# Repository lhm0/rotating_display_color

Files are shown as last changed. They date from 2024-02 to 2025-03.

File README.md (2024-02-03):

# Rotating Color Display

## Abstract: 
 The Rotating Color Display is a compact disc-sized device that rotates quietly using a CD motor. It features 56 color LEDs that display animated color images as well as time and weather data sourced from the internet. The device is wirelessly powered and controlled via a user-friendly web interface. It uses ESP32 and RP2040 microcontrollers, pre-manufactured boards, and is easy to assemble.
 
<p align="center"> 
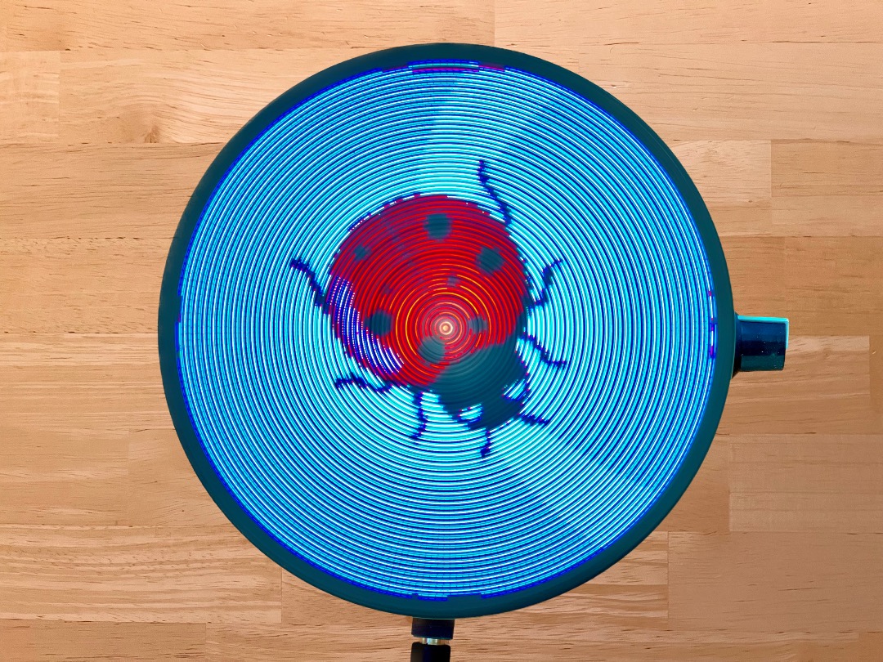
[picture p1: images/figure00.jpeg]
  
</p>

<p align="center"> 
<a href="https://youtu.be/7XahXYzULtI?si=OmdDaNnT-Jkq3F4Q" target="_blank">
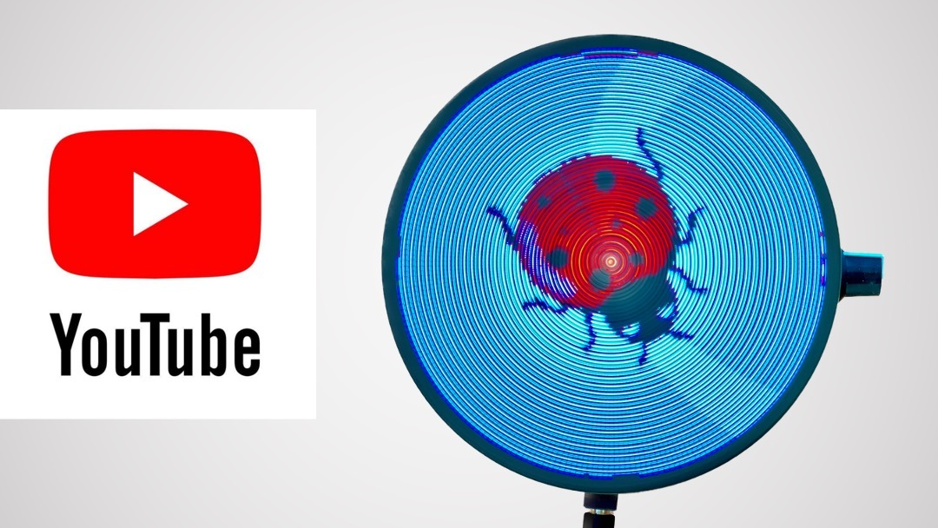
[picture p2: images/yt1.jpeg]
  
</a>
</p> 

## 1. Description of the device

The Rotating Color Display device comprises two primary units: a power supply unit and a display board (**figure 1**). Both are circular in design, with a diameter of 120mm, similar to the dimensions of a standard Compact Disk. The display board is rotated by a CD motor. Energy is wirelessly transmitted from the power supply unit to the display board, eliminating the need for wired connections.

<p align="center"> 
  
</p>

**Figure 1:  Rotating Color Display assembly.** The lower PCB is the power supply with wireless power transmission, the upper PCB is the display board.

The display board is equipped with a row containing 56 color LEDs. The LED operations are controlled by a RP2040 microcontroller, while an ESP32 microcontroller generates the display content. Images (including animated images) can be stored on and loaded from a micro SMD card. The ESP32 maintains a Wi-Fi connection to the internet.

This internet connection allows the device to retrieve the time from a time server, ensuring time accuracy. It also allows for the acquisition of weather data. Device operation is managed through a web interface (**figure 2**), accessible from any web browser. The interface allows users to manage login credentials, upload image files to the display, and control image and configuration files through a file manager.

<p align="center"> 
  
  
  
</p>
<p align="center"> 
  
  
  
</p>

**Figure 2:** The **web user interface** allows for operating mode selection and device configuration.

## 2. Operating modes

When switched on, the device tries to connect to a known wifi. If no valid wifi credentials are found, the unit will be configured as wifi access point. In this mode, a computer or mobile device can be connected, directly (SSID: RD40, no password). 

Once the wifi connection has been established, the unit will display its IP address on the  home page of the device (**figure 3**). Enter this address in your web browser. This will load the web user interface and will allow you to configure your local wifi.

<p align="center"> 
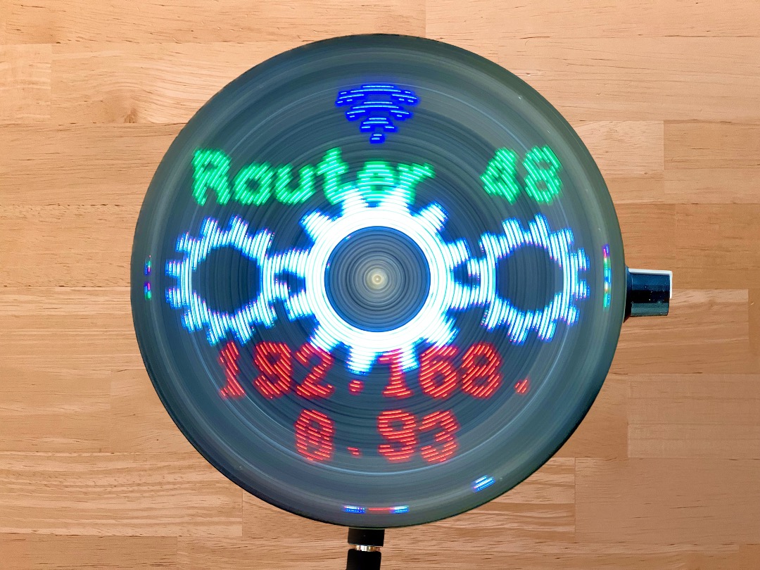
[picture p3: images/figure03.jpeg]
  
</p>

**Figure 3: home page.**

There are several operating modes that display time and weather information (**figure 4**). The logo clock mode integrates a customizable image into the clock face. The image can be easily uploaded from the user interface. The same is true for the analog clock, which uses a customizable clock face in the background.

<p align="center"> 
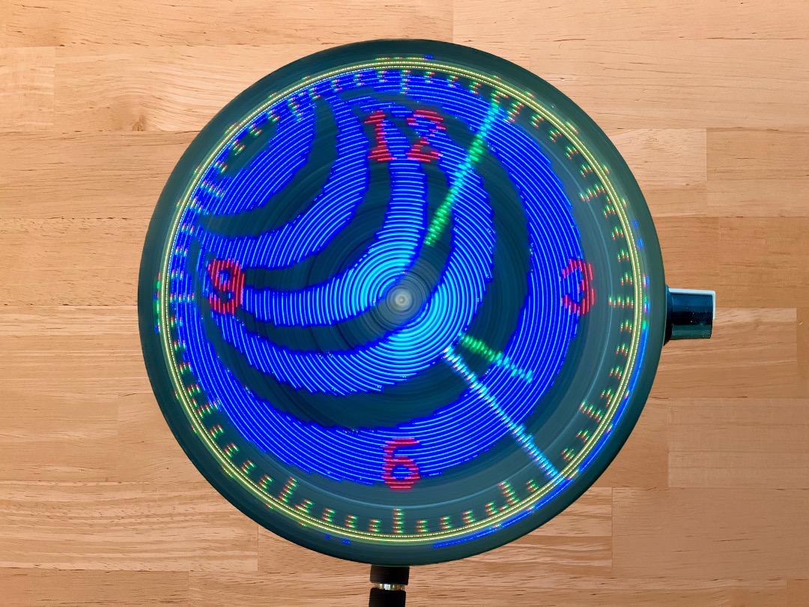
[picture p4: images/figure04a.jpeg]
  
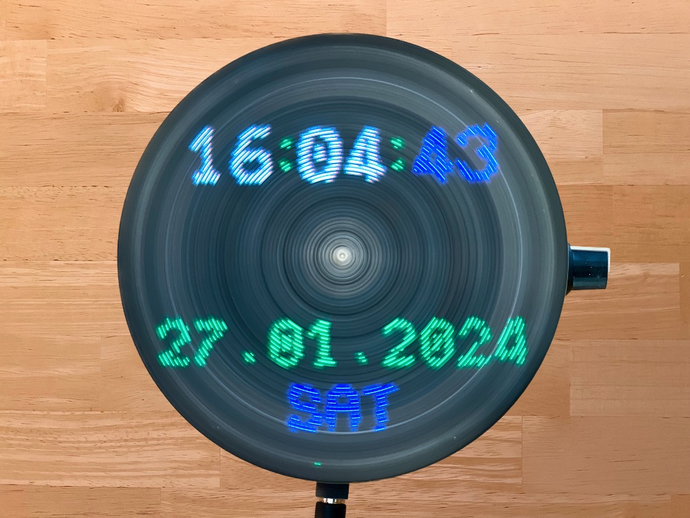
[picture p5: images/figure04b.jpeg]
  
</p>
<p align="center"> 
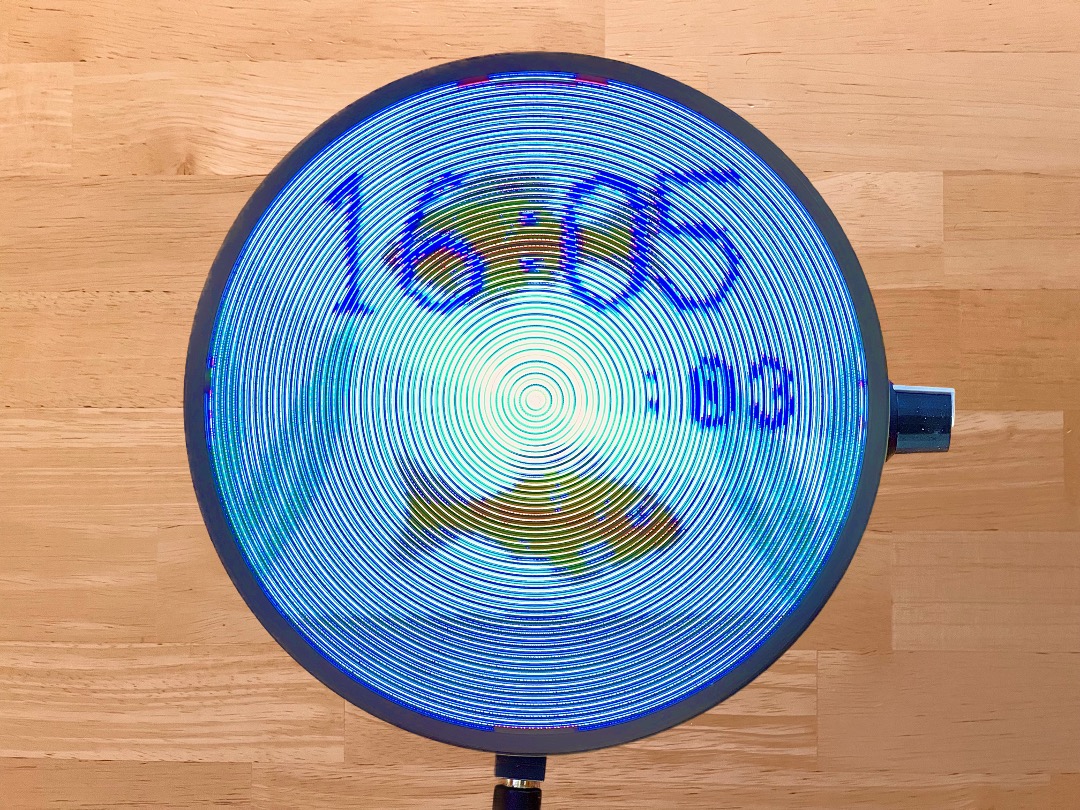
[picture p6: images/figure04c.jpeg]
  
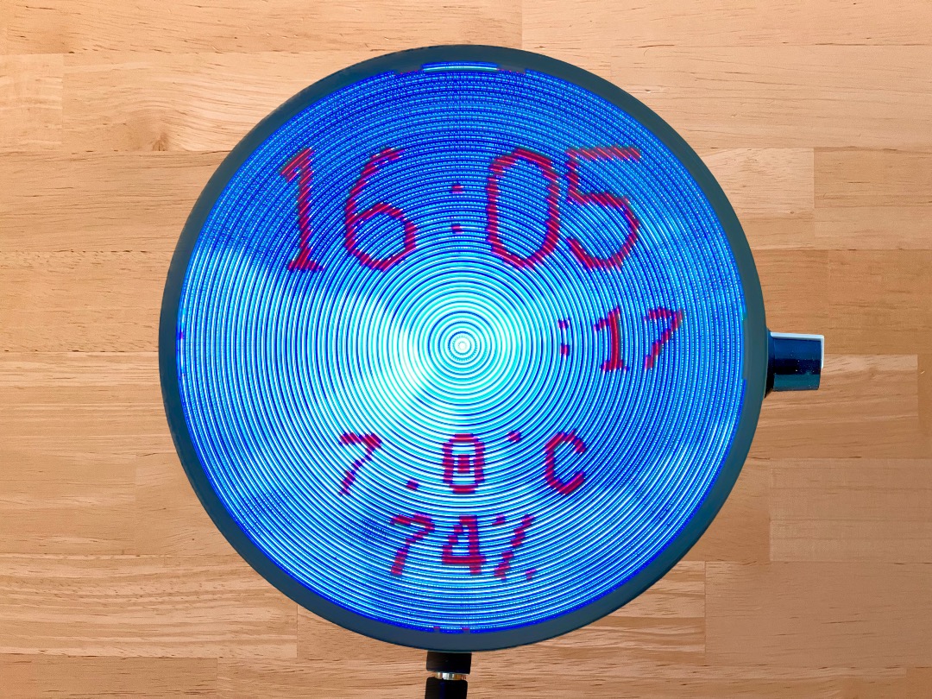
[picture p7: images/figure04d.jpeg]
  
</p>

**Figure 4: operating modes.** Modes can be selected and configured through the web interface.

## 3. Mechanical design

The device consists of two assemblies: power supply and display. The power supply board is also the base plate, which can either be placed on a flat surface or hung on a wall. A standard CD motor is attached to this board so that the CD tray above the power supply board can accommodate the display assembly. The display board is fixed with two M2 x 6 mm screws. Furthermore, the base plate carries a potentiometer to control the motor speed as well as an on/off switch for the motor.

<p align="center"> 
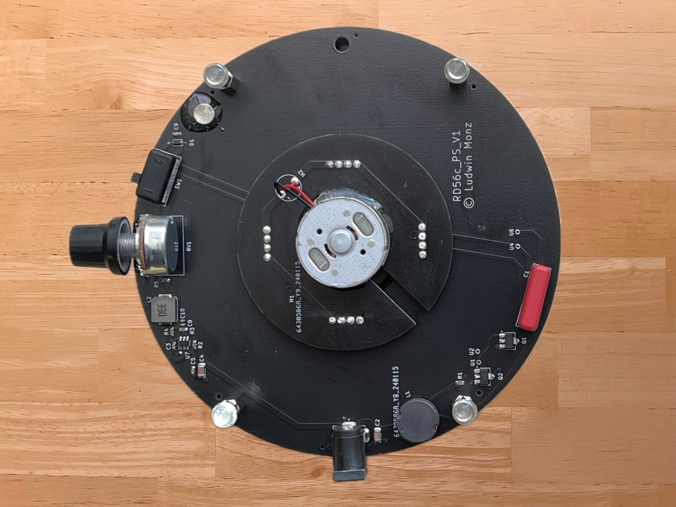
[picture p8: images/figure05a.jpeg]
  
  
</p>

**Figure 5: Power Supply Board** with CD motor (middle), 12 - 24 V power jack (lower side), and speed potentiometer

An important requirement for the display board is that the center of mass of the unit is exactly in the middle, on the axis of rotation of the motor. This is the only way to ensure smooth and vibration-free running of the display. To achieve this, the electronic components are arranged symmetrically in three groups (**figure 7**). In the first group the components are arranged symmetrically to a vertical axis. This initially ensures that the center of gravity lies on this vertical axis. However, since the components cannot be distributed symmetrically to the horizontal axis of symmetry, the center of gravity must be shifted to the center along this axis using balancing weights. For this purpose, two M3x6mm screws with two nuts each are placed to the right and left of the ESP32 antenna. The second group of components is arranged symmetrically in respect to the center point of the disk and does not need a balancing weight, therefore. The third group, however, does need a balancing weight (M3 x 6, 1 nut) in the 4:30 position of the disk.The overall balancing result is very good, but can certainly be further optimized.

<p align="center"> 
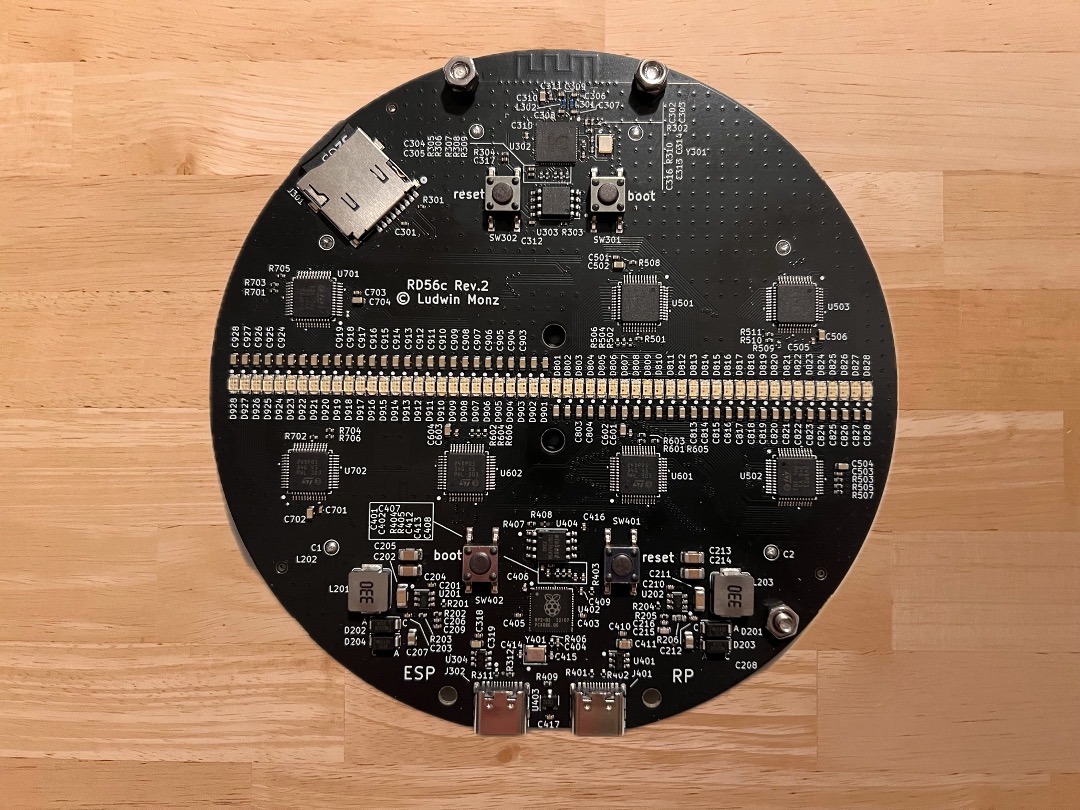
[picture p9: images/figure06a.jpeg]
  
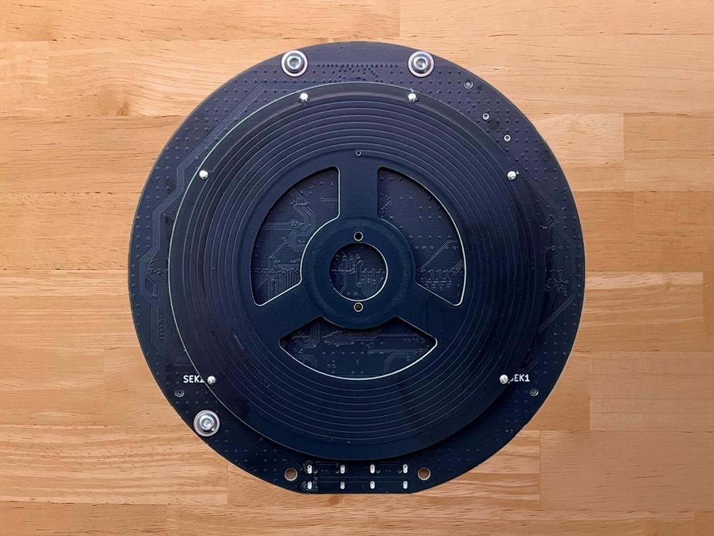
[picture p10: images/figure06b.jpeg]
  
</p>

**Figure 6: Display Board.** Main components are the two LED rows, five serial shift register chips, and two microcontrollers (Arduino nano and ESP-01s). On the backside of the board the secondary coil of the wireless power supply is attached.

<p align="center"> 
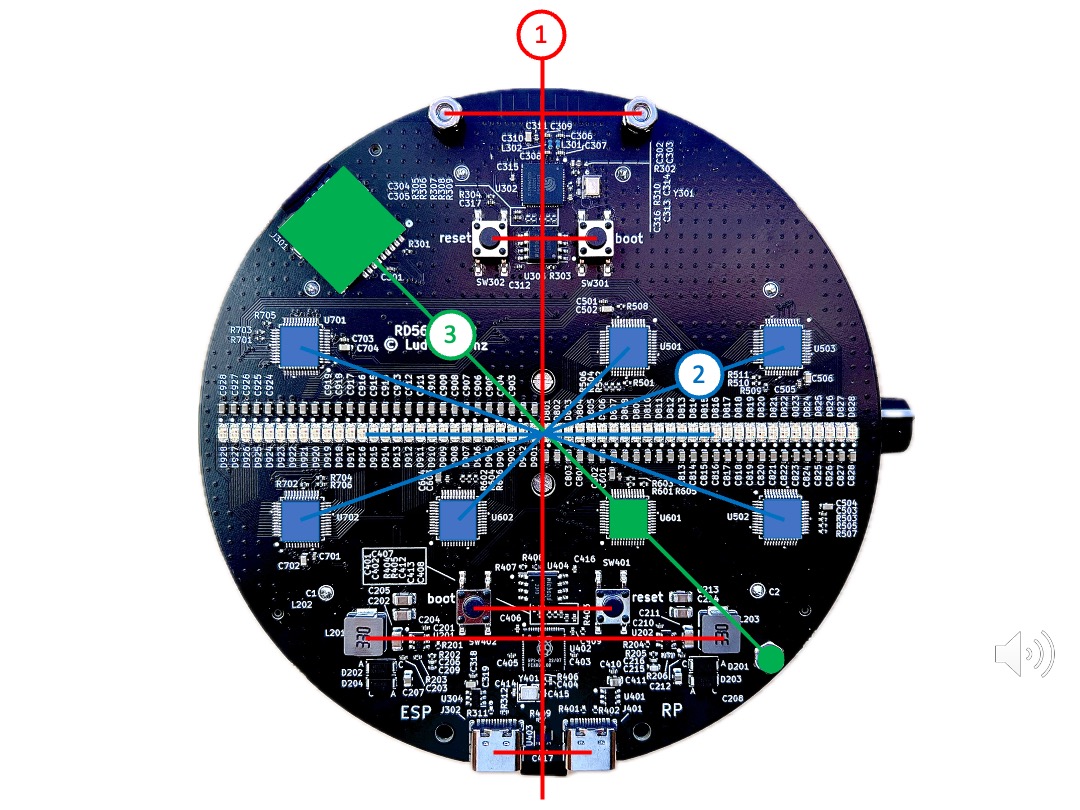
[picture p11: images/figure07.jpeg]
  
</p>

**Figure 7:** The components of the display board are arranged symmetrically in three groups. Balancing weights are used in group 1 and 3 to shift the center of gravity to the middle of the disk.

The LED row consists of 56 discrete, rectangular LEDs. The components each have a width of 1.6 mm and can be lined up with little spacing. The center of the LEDs is in a 2 mm grid. However, the row of LEDs is not arranged symmetrically to the center of the disk, but shifted by 0.5 mm. If the display panel is rotated by 180 degrees, this decentration causes the LEDs to be shifted by exactly 1 mm from the original grid (**figure 8**). This results in rotational interlacing: the radial resolution is increased from 2 to 1 mm. At the same time, the perceived frame rate also increases by a factor of 2..

<p align="center"> 
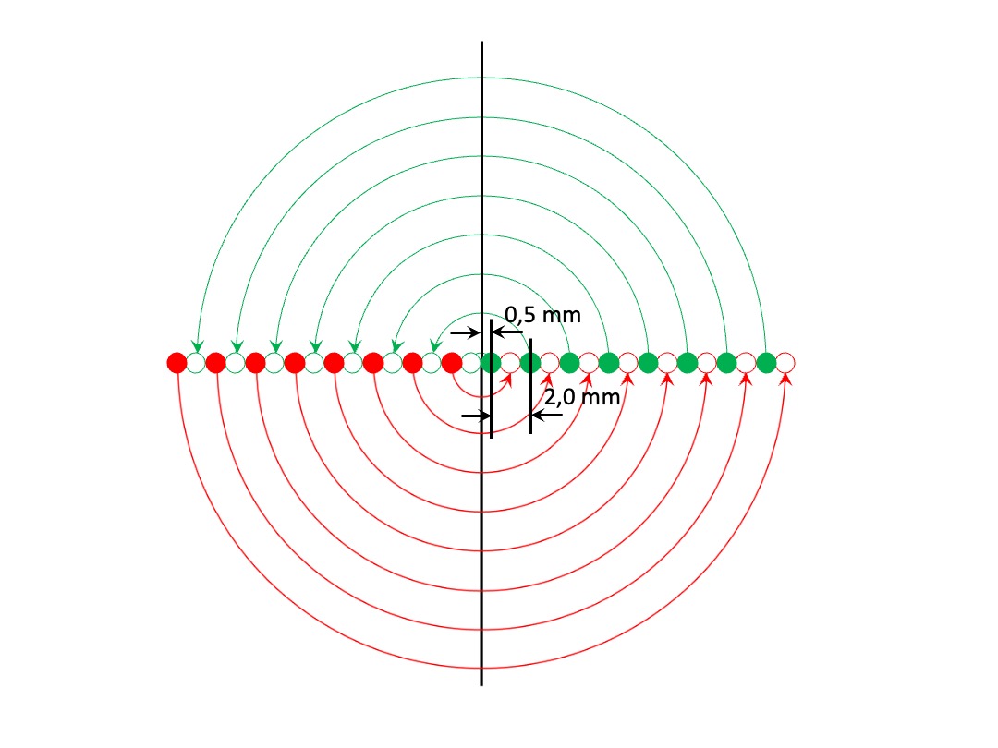
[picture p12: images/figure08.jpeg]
  
</p>

**Figure 8:** The LED row is shifted radially by half a LED width. The two halfs of the row generate an interlacing effect, which doubles both the radial resolution and the image frame rate.

The LEDs must output the image information at exactly the right position with each rotation. For spatial alignment of the image, a trigger signal is generated at a defined position for each rotation, which triggers the sequential, clocked output of the pixels. The trigger signal must be spatially very stable, otherwise no smooth image can be generated. It turned out that a Hall sensor is best suited for this purpose. It is located between the two USB-C connectors (see **figure 6**, left picture, bottom edge of the PCB). The magnet is glued into a hole of the power supply PCB (see figure 5, right picture, 2 o'clock position).

## 4. Electronics architecture

The distribution of the electronic circuitry between the two assemblies is shown in **figure 9**. The power supply assembly contains a Royer converter for wireless power transfer to the display assembly and an adjustment of the motor speed. The 56 color LEDs of the display assembly are controlled by 7 shift registers (24 bits each), which in turn are supplied with clock and data by a RP2040 microcontroller via an SPI interface. The displayed content is generated by an ESP32-S3 microcontroller, which is connected to the internet via Wifi. Furthermore, image data can be loaded from a micro SD card. The ESP32 transmits its data to the RP2040 via a SPI interface.

<p align="center"> 
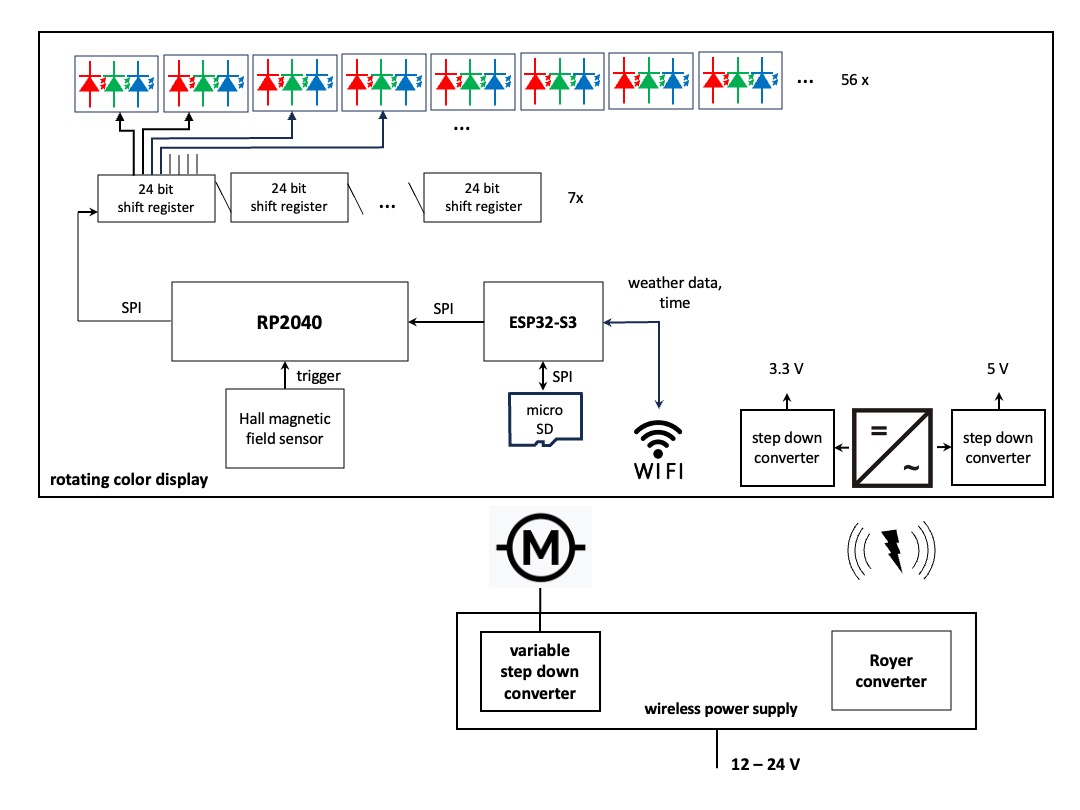
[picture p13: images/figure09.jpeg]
  
</p>

**Figure 9: electronics schematics.**

## 5. Power supply board

The core of the power supply is a Royer converter for wireless power transfer. An excellent article on the operation and design of the circuit can be found at Mikrocontroller.net (German) and the circuit was taken from there. Two transistors are alternately switched (push pull operation) so that a current flows through one half of the coil at a time. The coil belongs to a resonant circuit with a resonant frequency of about 120 kHz. The control voltage for the transistors is obtained via a coupling coil (**figure 10**). The secondary coil is located below the display board (see **figure 6**, right).

The Royer circuit uses very few components. However, the coil is quite complex. It is a bifilar coil, where the two halves are interleaved. In addition, the coupling coil must be connected with the correct polarity, otherwise the two transistors will be destroyed. In the early stages of development, the coil was wound with copper wire. However, this solution was quite difficult to reproduce, so in the final design the coils (bifilar primary coil, coupling coil, secondary coil) were implemented as a printed circuit (see **figure 5**, right and **figure 6** right). The circuit was found to have surprisingly high and perfectly adequate transmission efficiency, although the quality factor of the printed coils is inevitably compromised. The Royer converter with the printed coil assembly is absolutely safe to rebuild.

The Royer converter can be supplied with 12 to 24 V. Depending on the voltage, the transferred power can be increased. This allows the operation of the display at high brightness. However, even with 12 V supply, the available power is sufficient for normal operation. 

<p align="center"> 
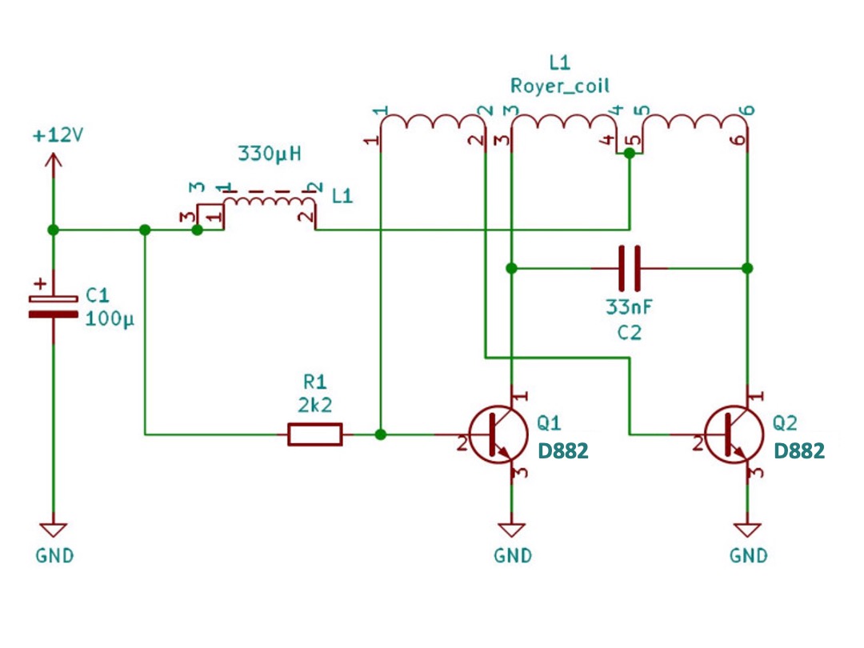
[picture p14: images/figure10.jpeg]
  
</p>

**Figure 10: Royer converter**. Compare Mikrocontroller.net for reference.

There is also a circuit for supplying the CD motor on the power supply board (**figure 11**). As the supply voltage can be vary from 12 to 24 V, a step down converter is used to generate a variable voltage between 1.7V and 6.0V, which can be adjusted via a potentiometer. The voltage range corresponds to the specified operating range of the CD motor. The supply of the motor can be interrupted with a switch, for example to allow programming of the microcontrollers.

<p align="center"> 
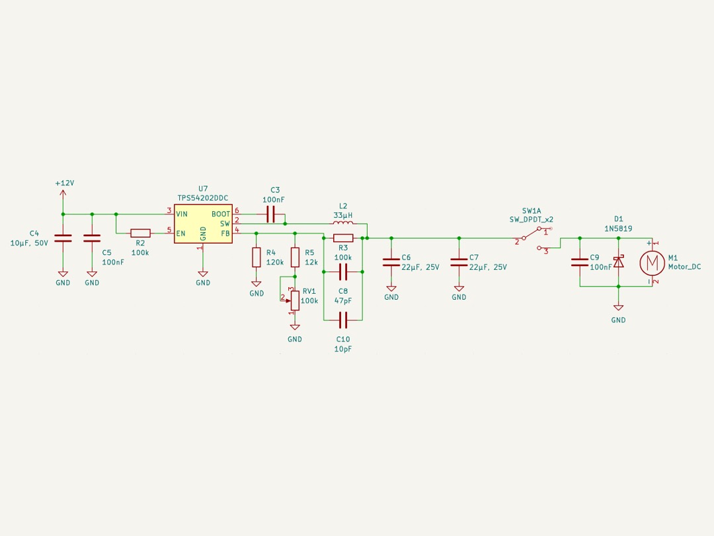
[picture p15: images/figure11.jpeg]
  
</p>

**Figure 11: variable voltage regulator** for driving the CD motor

## 6. Display Board

**a) The LEDs**

The 56 LEDs of the display board are driven by 7 cascaded 24-bit shift registers (**figure 12**). The registers load the serial data stream from one of the SPI interfaces of the RP2040. The microcontroller generates separate "LED enable" signal for the R, G, B LEDs, respectively. This allows for white balancing (not implemented yet). The STP24DP05BTR LED current sink controller sets the LED current to 20mA each. The maximum current per register would therefore be 480mA, if all LEDs were on, simultaneously and continuously. Theoretically, the current of the 56 LEDs could add up to 3.3A, which, at 5V, would correspond to 16.5 W. This is significantly beyond the capability of the wireless power supply. However, the current can be controlled by the RP2040 microcontroller by setting the duty cycle appropriately.

<p align="center"> 
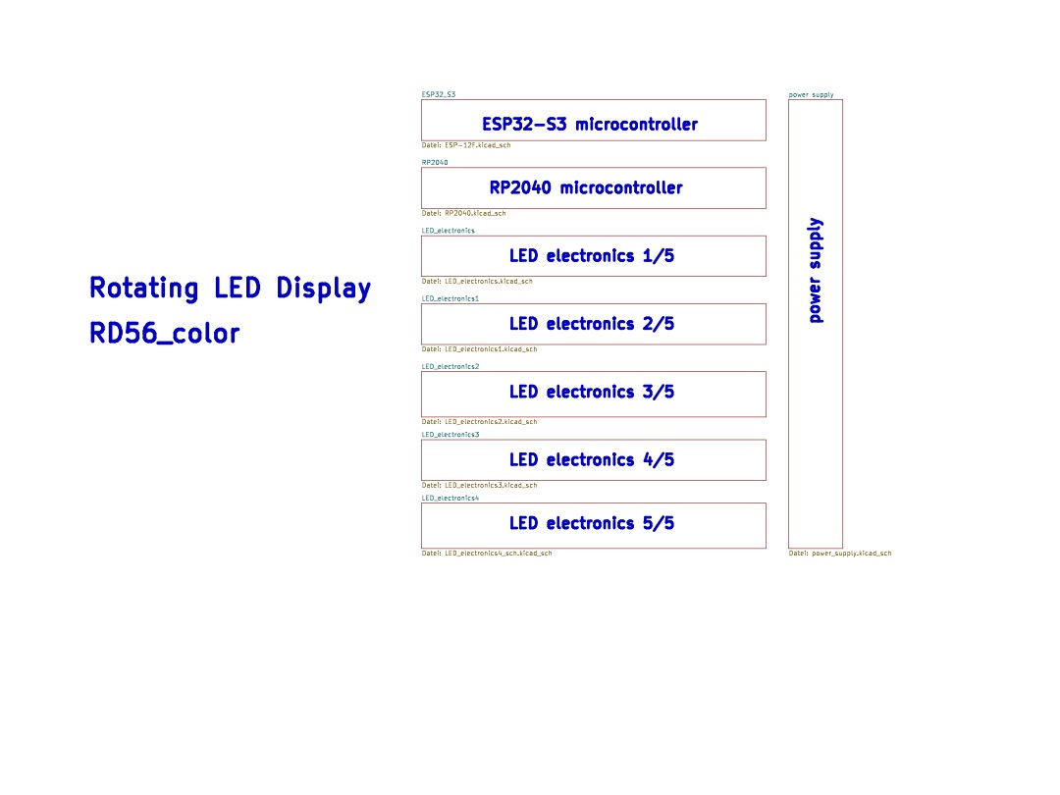
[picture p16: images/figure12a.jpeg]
  
</p>
<p align="center"> 
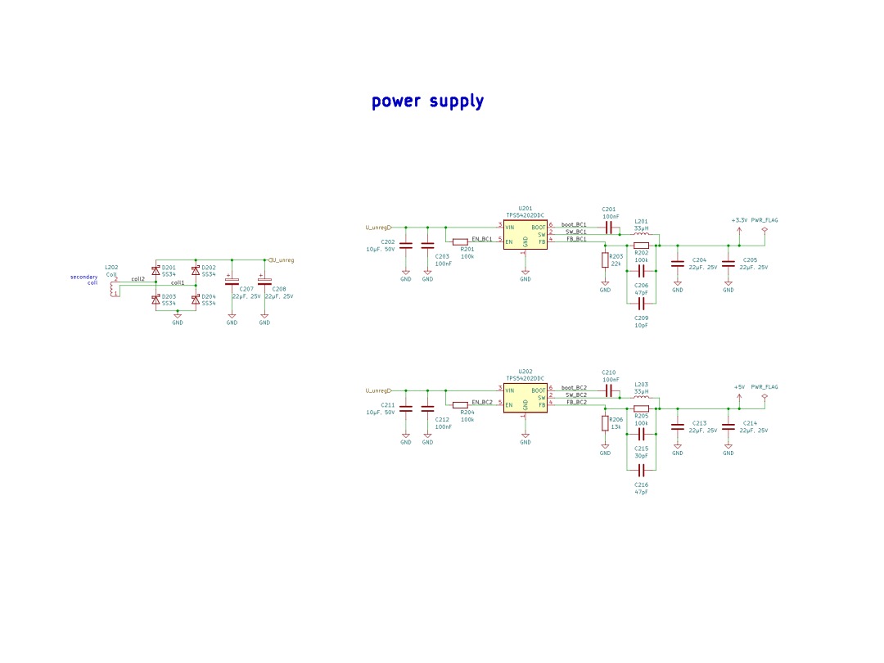
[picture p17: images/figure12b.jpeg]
  
</p>
<p align="center"> 
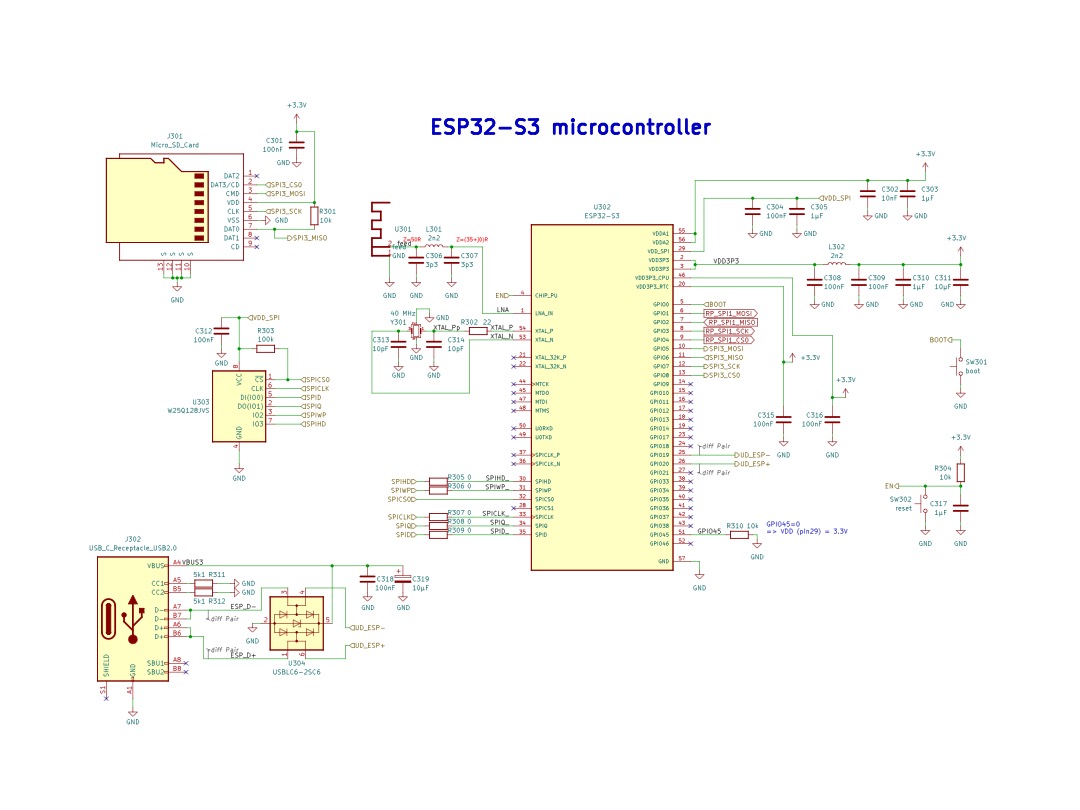
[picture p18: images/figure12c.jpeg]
  
</p>
<p align="center"> 
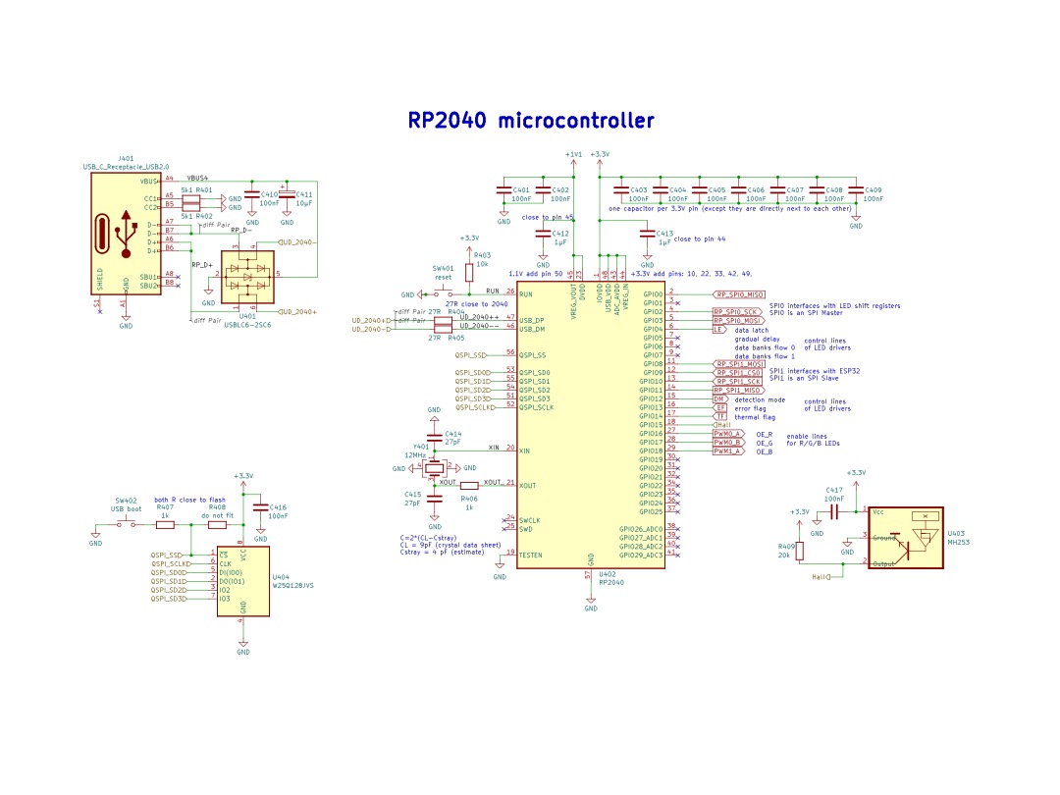
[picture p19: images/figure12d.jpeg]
  
</p>
<p align="center"> 
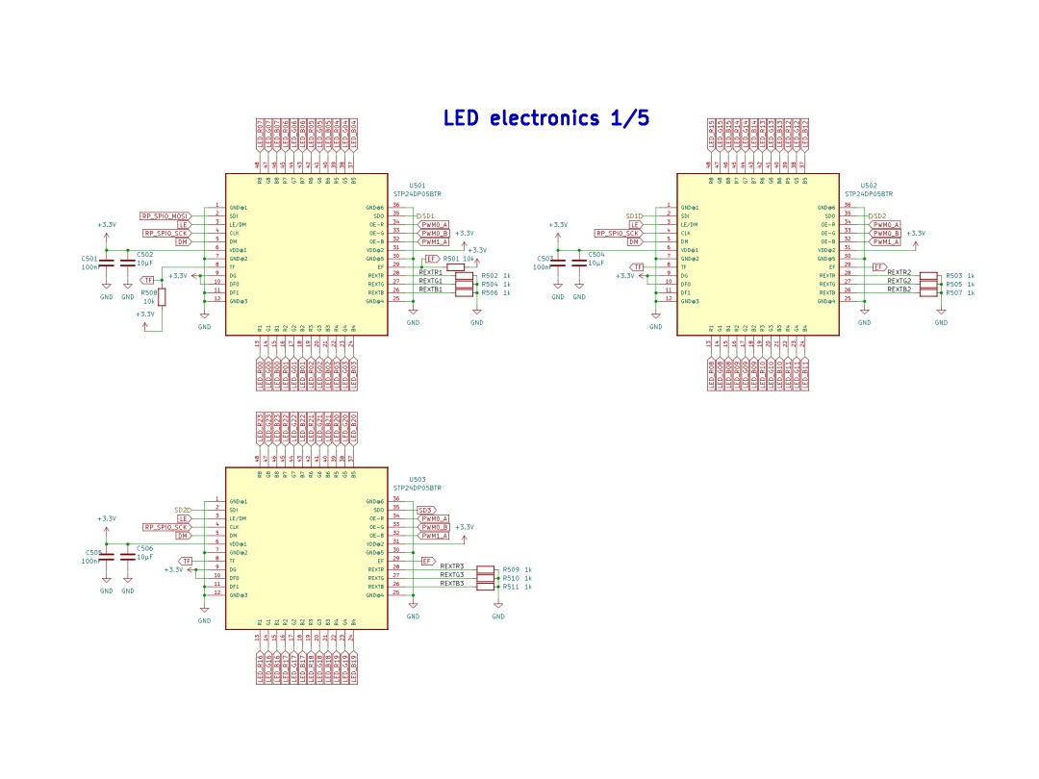
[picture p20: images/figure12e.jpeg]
  
</p>
<p align="center"> 
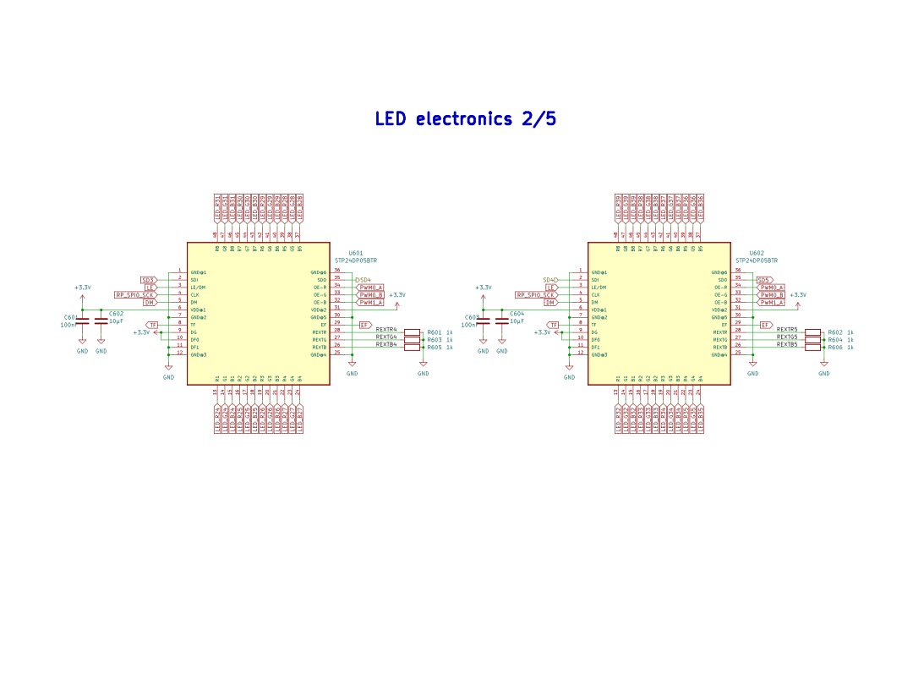
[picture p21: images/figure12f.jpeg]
  
</p>
<p align="center"> 
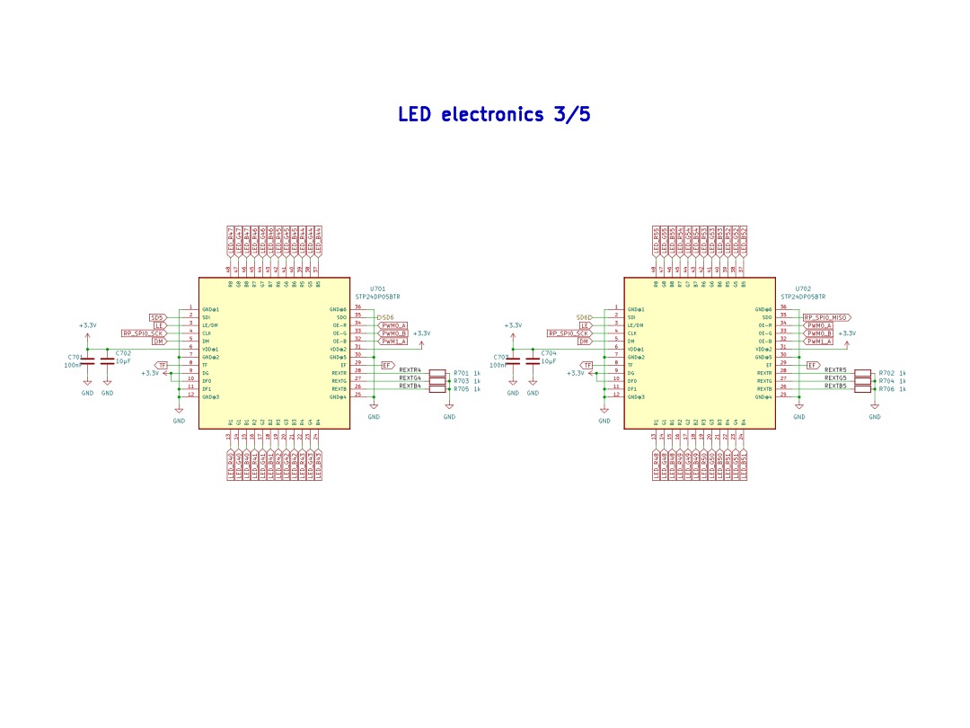
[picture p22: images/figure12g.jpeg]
  
</p>
<p align="center"> 
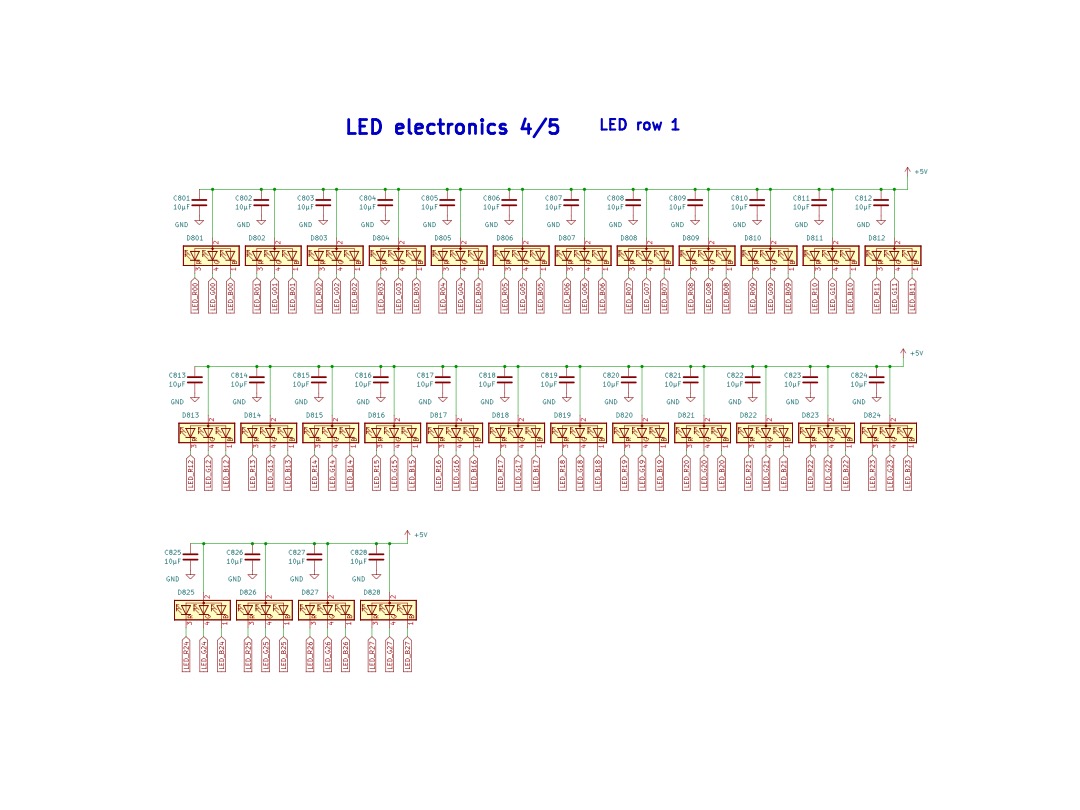
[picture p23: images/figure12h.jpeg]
  
</p>
<p align="center"> 
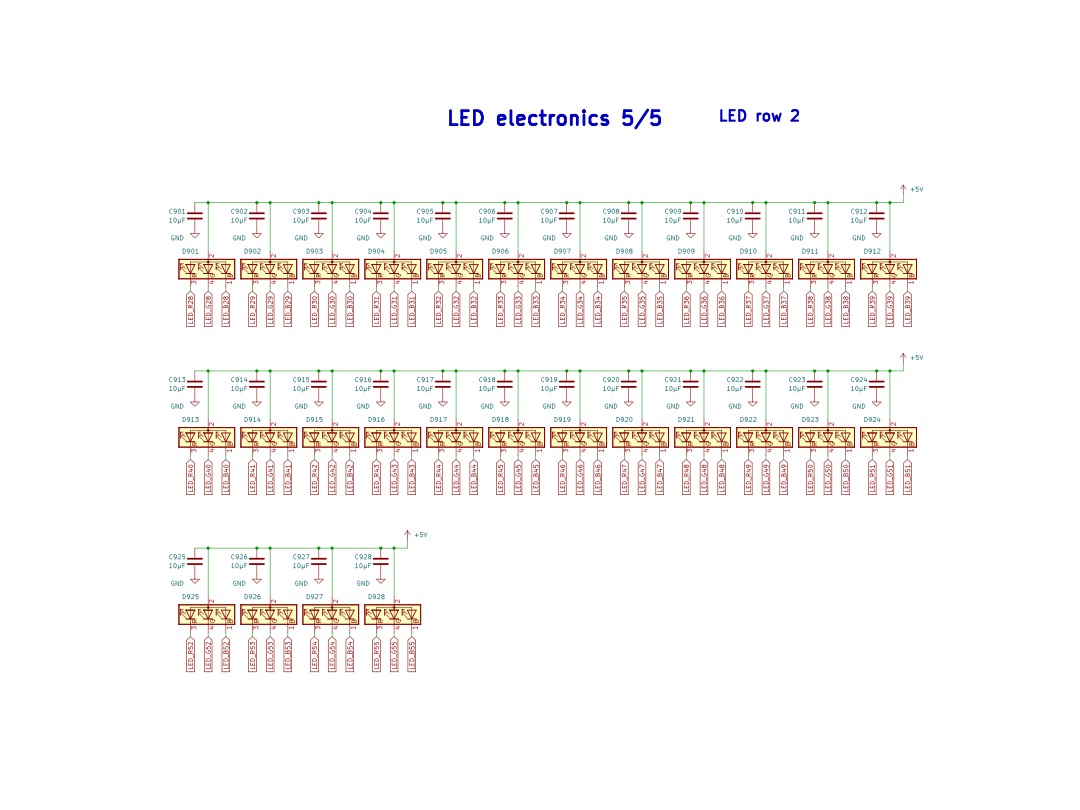
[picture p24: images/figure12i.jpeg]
  
</p>

**Figure 12: circuit diagrams of the display board**. Diagrams also available as download and on Github.

**b) Displaying color**

Displaying color is based on additive color mixing. The three primary colors, red, green, and blue are mixed with different intensities. For example red and green combined at equal intensity make yellow. However, the circuit only allows the LEDs to be either on or off. Intensity can only be set using pulse width modulation. In order to synchronize PWM with the rotation of the disk, each pixel is devided into 8 sub-pixels (**figure 13**). This allows for setting the intensity in 8 steps for red, green, and blue, respectively. The color space can be displayed with 8 x 8 x 8 = 512 colors.

<p align="center"> 
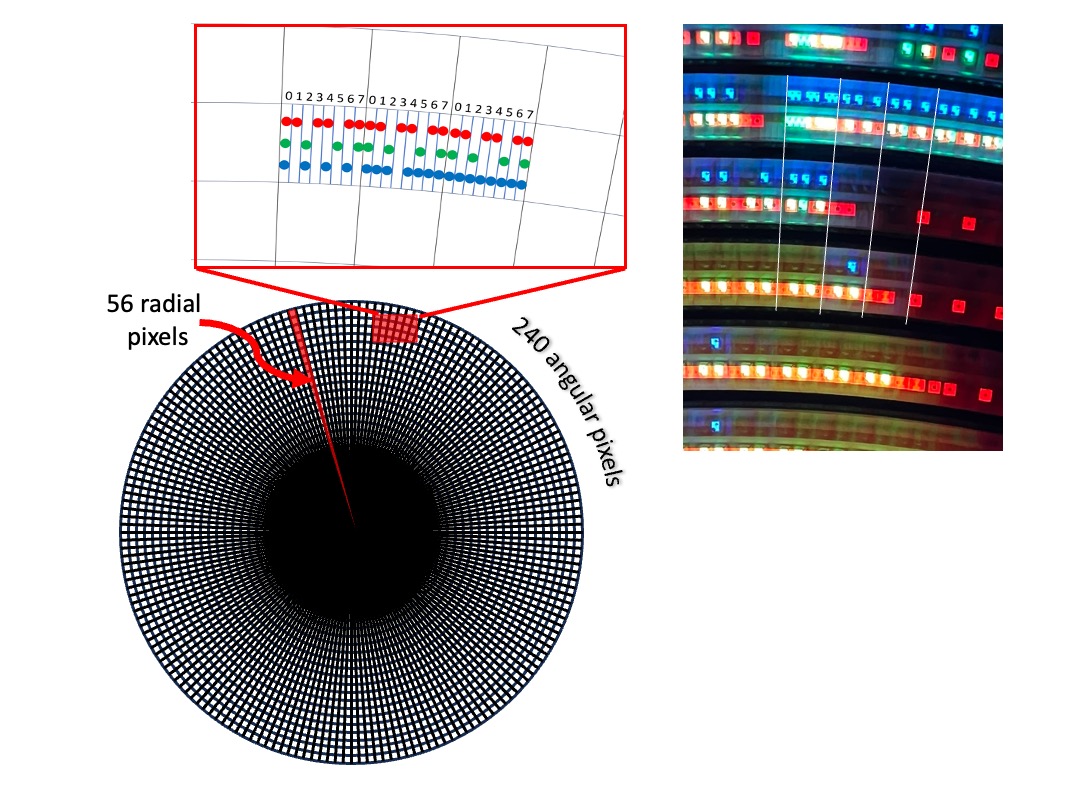
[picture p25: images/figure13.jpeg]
  
</p>

**Figure 13: displaying color**. each pixel is divided into 8 sub-pixels. This allows for pulse width modulation of the LED intensity. The intensity resolution is 8 steps for red, green, and blue, respectively. On the right hand side there is a photo of some of the pixels of the running display.

**c) RP2040 interrupts and timing**

The SPI interface is operated with a clock rate of 25 MHz. The 168 bits (56 RGB LEDs, 3 colors each) are therefore transferred in 168 x 1/25MHz = 6.7µs. Assuming a maximum rotation speed of the display of 1200 RPM, this corresponds to 50ms per revolution. At one full rotation of the display 240 pixels with 8 sub-pixels each are output per LED. This corresponds to 26µs per sub-pixel. Thus, the transmission time via the SPI bus (6.7µs) is significantly shorter than the display time per sub-pixel.

The idea of using two microcontrollers (RP2040 and ESP32-S3) is essentially to separate the very time-critical timing of the LED control from the computationally intensive and asynchronous image generation and internet communication. In this way, the RP2040 is relieved to the maximum and the display of the image is extremely stable.

The software of the RP2040 programmed in C consists of two short interrupt routines. The first routine ("HallIRQ") is triggered by the Hall sensor exactly once for each full rotation (**figure 14**). This routine starts a timer, which sets the duration for which a single row of 56 color pixels is displayed. Once the timer expires, it is automatically restarted and a second interrupt routine is triggered ("PixelIRQ"). In this second routine the bit pattern of the LEDs is updated. So in this way a new LED pattern appears with each expiration of the timer. It is important that the timer restarts automatically (hardware controlled). Otherwise there could be a delay if the processor cannot start the interrupt routine immediately (because another routine prevents this, for example).

Another important function is to set the duration of the timer 1 so that exactly 240 x 8 = 1920 pixel rows per turn are output. For this purpose, the variable "tpt" (time per turn) is increased by the set value of the timer with each call of PixelIRQ. The routine HallTRQ can read tpt and thus knows the exact time duration for one revolution - even if it consists of more or less than 1920 timer cycles. The new time per pixel (tpt/240) is then calculated from this value and the timer is set accordingly.

To control the image brightness of the red, green, and blue LEDs, the threshold function of the timer is used: as soon as a programmable threshold for R, G, and B is exceeded, an output of the RP2040 switches. The three signals are used to switch on the respective LEDs for the selected time. Controlling the brightness of R, G, and B separately allows to adjust the relative brightness of the three channels and therefore to shift the white point and thus color balancing the display. However, it has turned out that the LEDs are calibrated such that a reasonable "white" is achieved when the LED current is set to 20 mA for the three LEDs, respectively.

<p align="center"> 
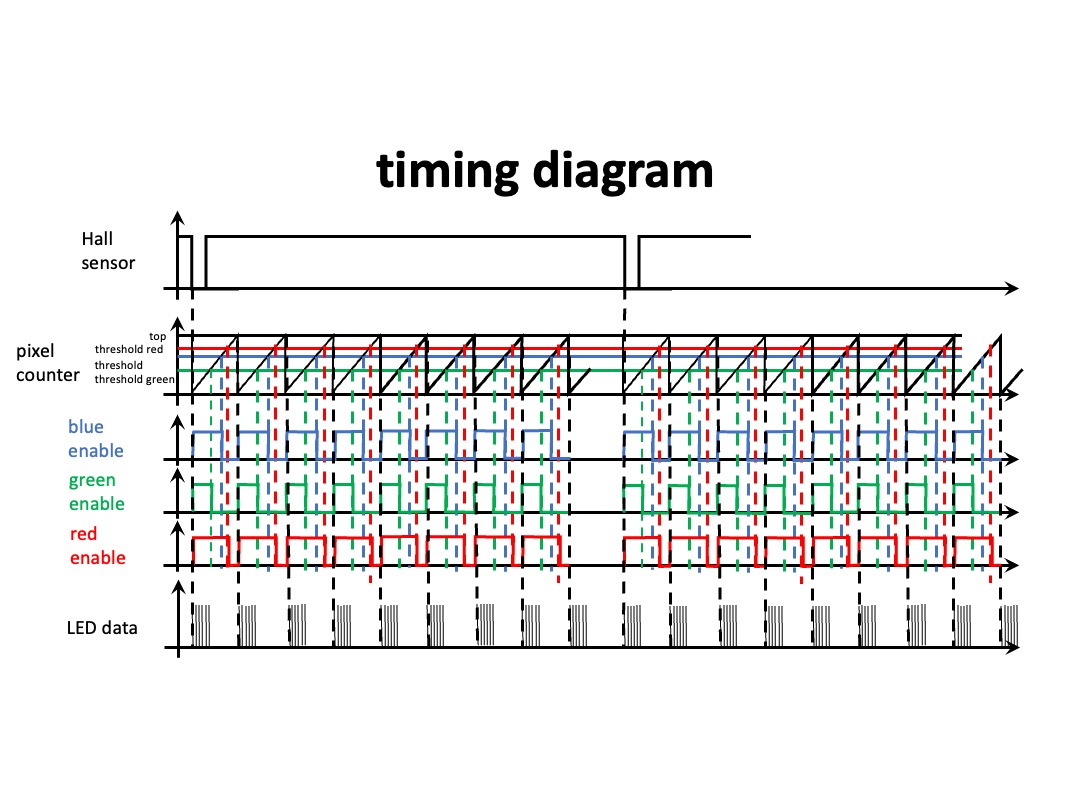
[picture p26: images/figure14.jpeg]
  
</p>

**Figure 14: RP2040 interrupt timing.** The timer clocks the pixel output and sets the LED brightness.

**d) ESP32-S3 for Internet communication and image generation**

The microcontroller ESP32 has a Wifi module for internet communication. The antenna of the controller is placed at the edge of the display board, because the interference field of the wireless power supply is lowest there. 

Although a concern in the beginning of the development, it turned out that the fast rotation of the display does not lead to any noticeable impairment of the Wifi connection.

**e) Programming of the microcontrollers**

The RP2040 can be programmed via a USB-C socket. During programming the power supply of the display needs to be on. Should there be a connection problem between the RP2040 and the programming computer, it helps to start the controller in boot mode. In order to do so, push and hold the RP2040 boot button while powering on the device. Once power is on, you can release the button.

Programming the ESP32S3 via its USB-C connector is easy and reliable as well. There is also a boot button, which can be used for initializing the controller.

Please note that the HTML, CSS and JS code of the user interface webpages has to be loaded onto the micro SD card. Make sure to properly formate (FAT16) the card before copying the data. You need to copy all files and folders in the "data" subfolder of the ESP32 directory of the repository to the root level of the SD card. When done, there. should be the folders "html", "variables", and "images" on the highest level of the SD card. 

# 7. The Software of the ESP32

The ESP-32 handles the generation of the image data and its transmission to the RP2040 (rouphly 10 times per second). The displayed information (time and weather data) is retrieved from the Internet or read from the SD card (still images and animated images). Furthermore, the microcontroller serves as a simple HTML web server that can be accessed by any browser to control the display.

**a) Generation of the image data**

Even though the resolution of the display achieved with the 56 color LEDs is relatively low, it is sufficient to display images and text upright, undistorted and therefore easily readable. The image data is generated in a rectangular pixel matrix (i.e. a cartesian coordinate system) with 110 x 110 pixels (**figure 15**). This bitmap then has to be transformed into the polar coordinate system of the rotating LED rows, before it is transferred to the RP2040. To make the transformation fast, a lookup table is used, which transforms the x,y coordinates of the bitmap into the r, theta coordinates of the rotating LED lines. The transformation also takes into account the alternating order of the LEDs between the two halfs of the row.

<p align="center"> 
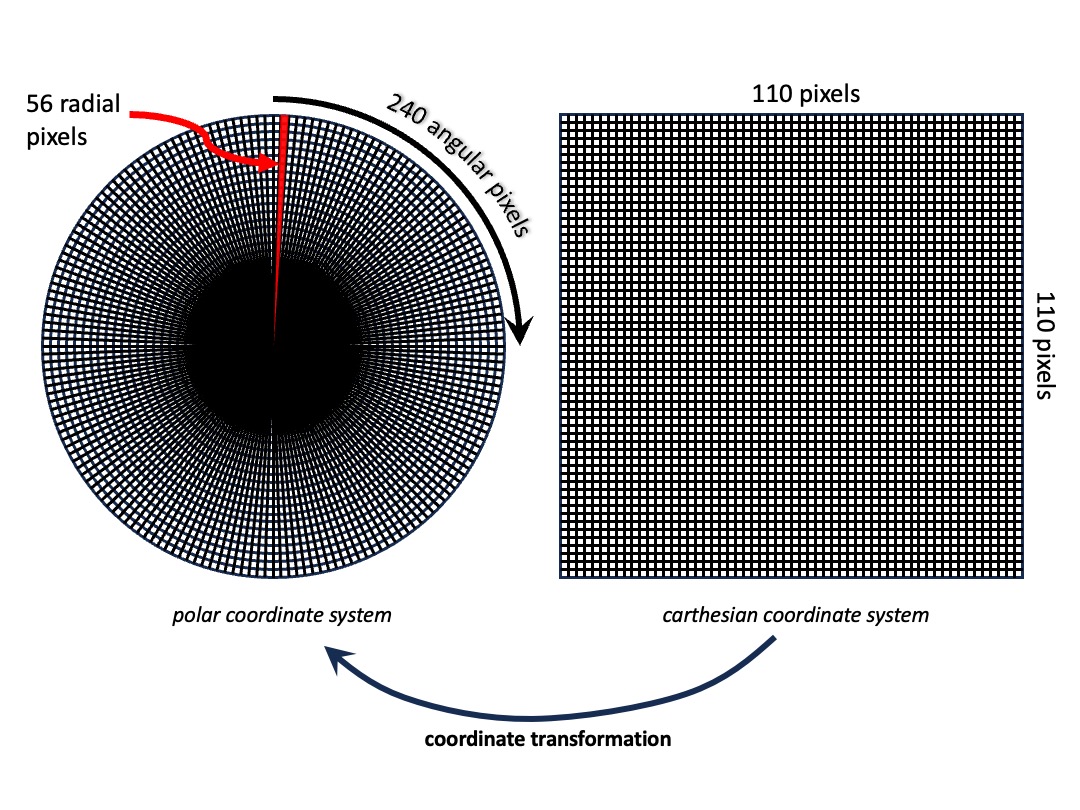
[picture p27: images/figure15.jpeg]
  
</p>

**Figure 15:** The display handles a **110x110 pixel bitmap**, which is transformed into the polar coordinate system of the rotating LED rows

**b) Control of the display via web interface**

For the implementation of the web server the library ESPAsyncWebServer is used. It has the advantage that the server activity runs in the background independent of other processes running simultaneously on the controller. The server retrieves the HTML, CSS and JS data of the displayed web pages from the SD card file system. Therefore, the web pages and the server can be implemented independently. Retrieving or modifying data is done using the HTTP GET and POST methods.

Certain parameters (brightness of the LEDs, operating mode of the display) can be set via the web interface. In addition, configuration data, such as the access data to the weather service openweather.org or the Wifi data can be edited and saved. These data are also stored in the file system of the SD card and are therefore also available after a reboot.

The user interface of the device has a file browser with which files can be uploaded from the end device (e.g. mobile device) to the SD card or downloaded from the SD card. This is especially usefull for loading image data to the device. In addition, files and entire directories can be deleted, renamed and moved. This simplifies the organization of the flash disk considerably.

Furthermore, the web interface provides a page for converting, uploading, and organizing images ("RDC Image Manager"). Still images can be uploaded in almost any image format and resolution. The software down scales and converts the images into the proprietary ".rdc" format ("rdc" = rotating display color). This format stores the color pixels sequentially, non-compressed, using 3 x 4 bits (1,5 bytes) per pixel. 

The RDC Image Manager can also deal with animated GIF files. As the image update rate is limited (about 10 images per second), there is an option to reduce the number of frames of the animated sequence. Please note, that saving an animated ".rdc" file might take a while, as the filesize can be substantial.

Known bug: the upload of animated ".rdc" files might lead to corrupt files, sometimes. The cause has not been clarified yet.

**c) Software architecture**

The ESP32 software is written in C++. In order to keep an overview despite the large amount of software, the function blocks and the data have been divided into classes. The following is a brief description of the most important classes:

Class RD40

The class provides the central rotating display object. It manages the (private) data of the displayed image (four bits per color and three colors per pixel). The class has methods for displaying bitmaps and for passing data to the display controller.

Class myBMP

This class creates 110x110 color bitmaps for display. It uses private methods to print text on the bitmap, draw lines and circles, or load images.

Class WebInterface

This class manages the web user interface. Once the webInterface object has been initiated, the web server will run in the background without the need for any attention from the software. The class provides certain attributes, such as clockMode and brightness, which are managed by the web interface. The user can change configuration data via the web interface. The data is then stored as parameter files on the SD card.

Not being a software engineer myself, the source code would most certainly benefit from a code review and revision.

**d) Development Environment**

Visual Studio Code with the PlatformIO extension was used as the development environment for both RP2040 and ESP32. The environment is much faster and more comfortable than the Arduino IDE. The ini files of the respective projects manages all settings, including libraries necessary for compiling. 
In addition, Visual Studio Code can also be used for the development of the source code of the web pages.

## 8. Reproduction of the rotating display

All necessary data, such as source code, circuit diagrams, printed board layouts, parts list and sources of supply are included either in this article or in my public github repository. They may be used for non-commercial purposes, such as by hobbyists or in education, whether for reproduction or further development. Either way, please respect the terms of the license.

The two main boards (display board and power supply board) can be manufactured based on the provided production data. The prototypes were manufactured and assembled by JLCPCB. The production data, including Gerber files, BOM, and component position files, are included in the repository. 

Some components need to be soldered manually, as they are through-hole-components. Please refer to the following description. The assembly is relatively simple, although some soldering skills are required. 

<p align="center"> 
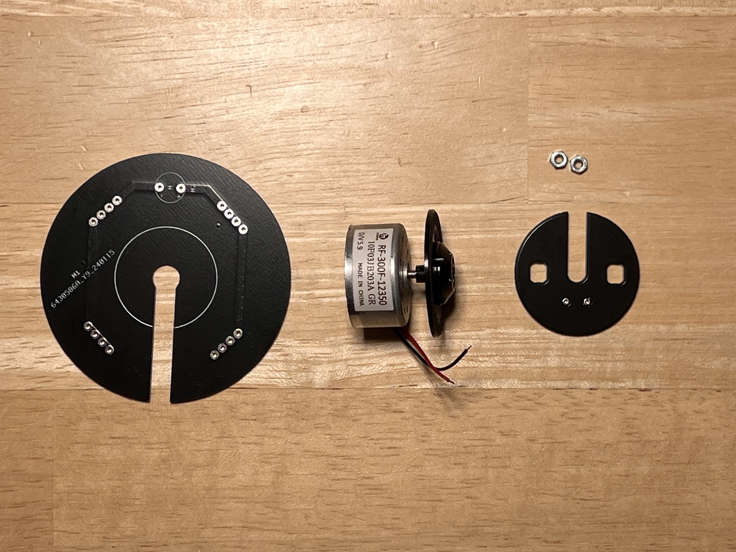
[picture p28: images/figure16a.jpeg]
  
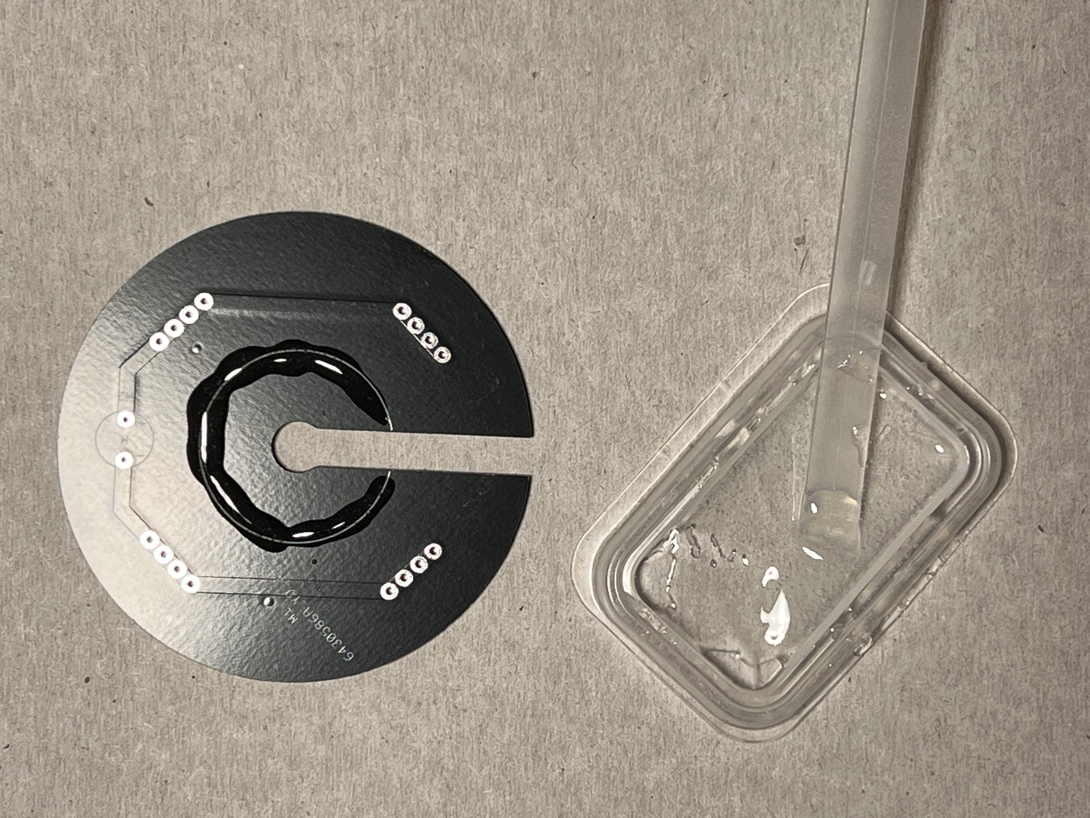
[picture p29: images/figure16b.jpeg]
  
</p>
<p align="center"> 
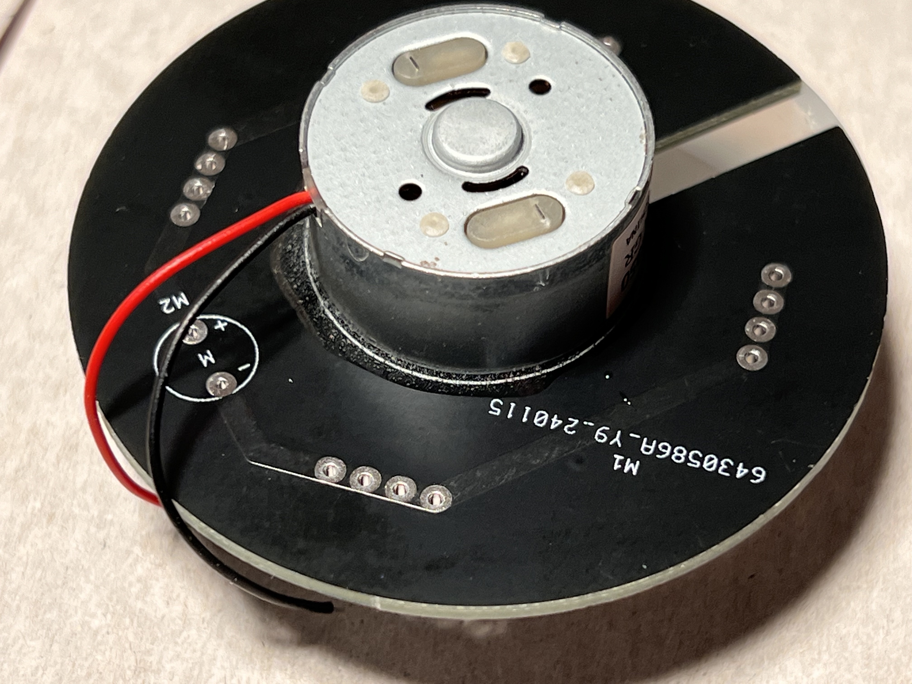
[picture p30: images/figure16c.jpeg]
  
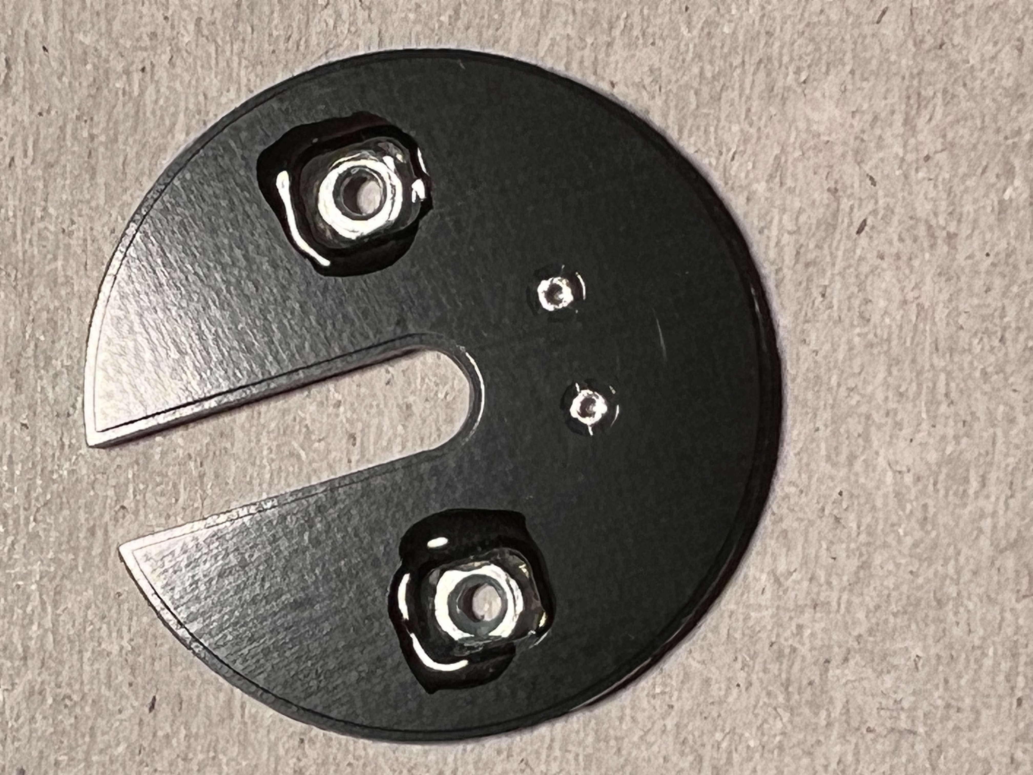
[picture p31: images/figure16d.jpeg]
  
</p>

**Figure 16:** Start with the assembly of the power supply board. Use fast curing two component epoxy resin to glue the CD motor to the carrier plate. Furthermore, carefully glue two M2 nuts to the CD tray auxilliary plate, without contaminating the threats.

<p align="center"> 
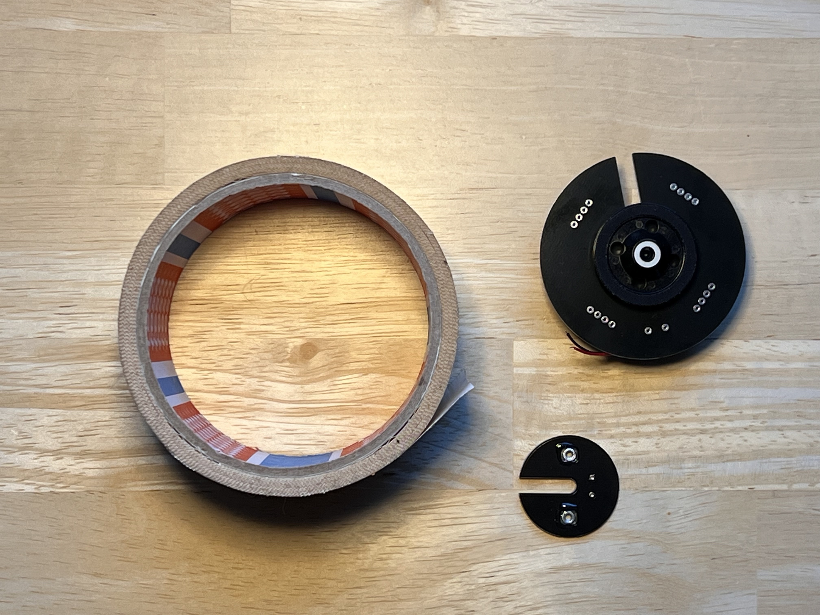
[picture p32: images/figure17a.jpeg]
  
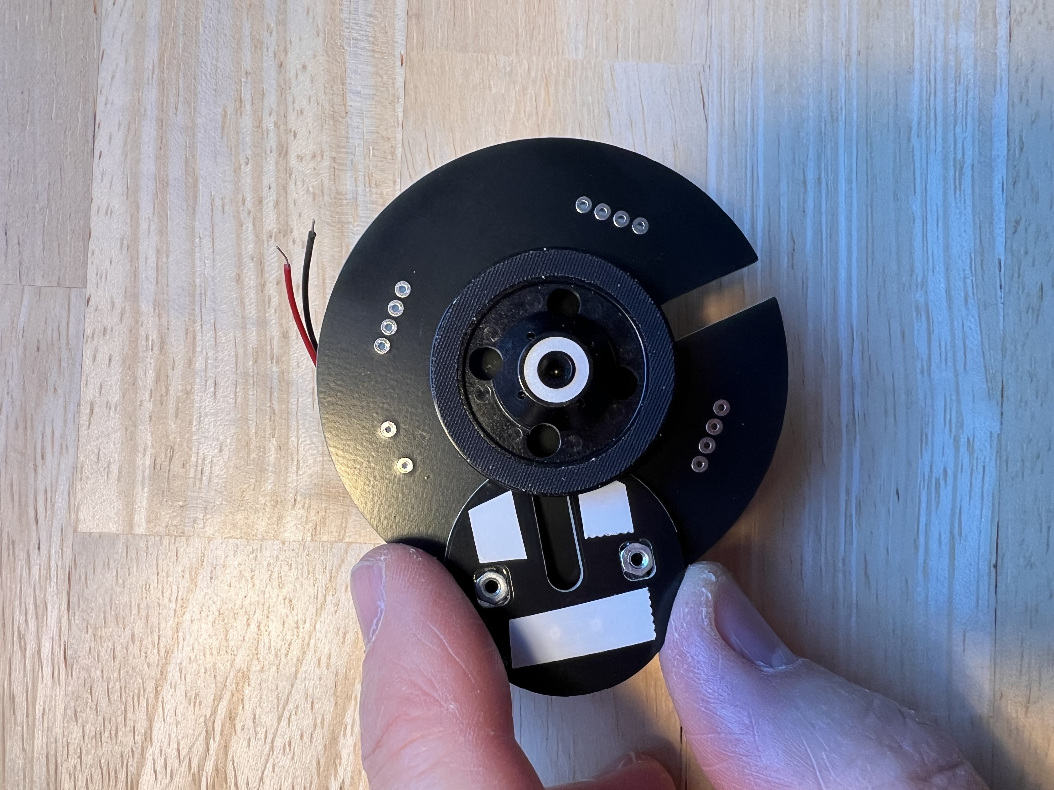
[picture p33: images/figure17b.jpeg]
  
</p>
<p align="center"> 
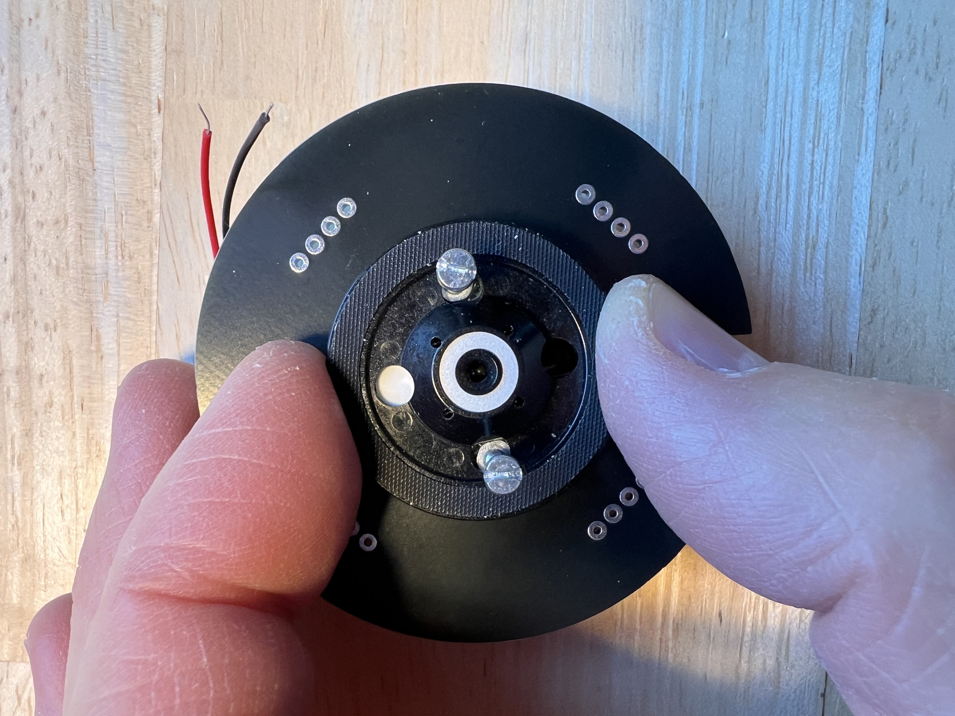
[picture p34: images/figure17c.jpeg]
  
</p>

**Figure 17:** Use double sided tape to attache the auxilliary plate with the two M2 nuts to the back of the CD tray. By means of two M2 screws you can make sure the plate is in the right position.

<p align="center"> 
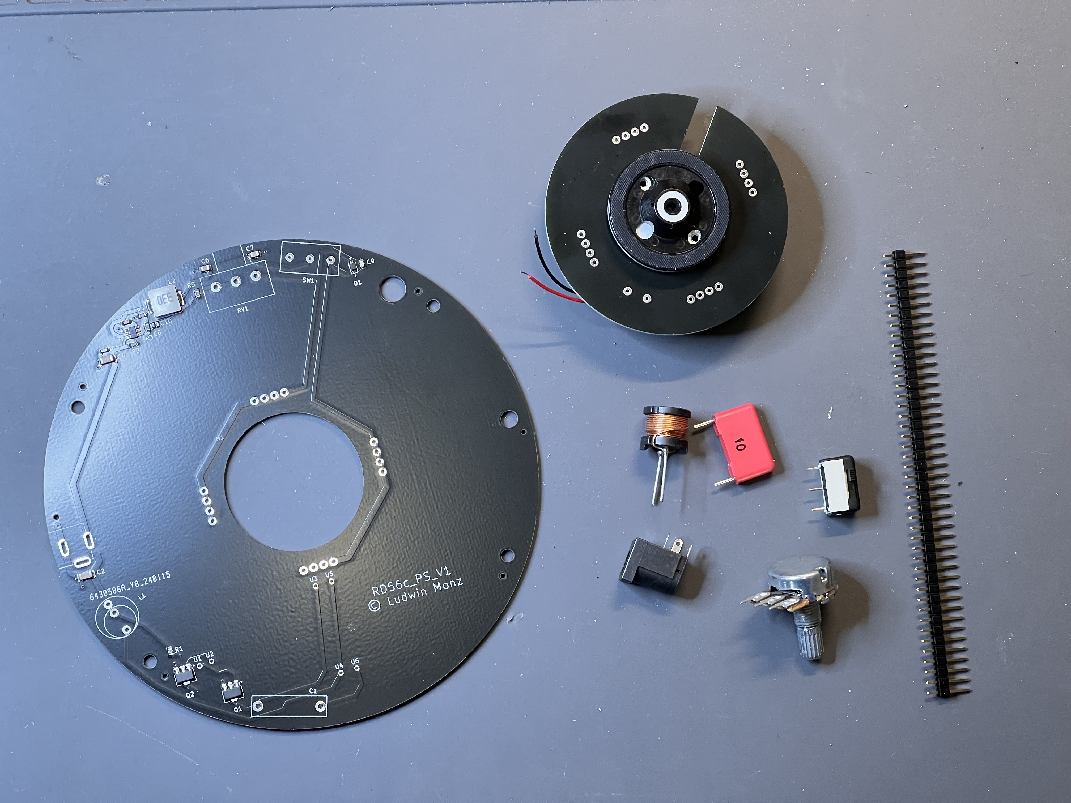
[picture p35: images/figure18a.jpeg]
  
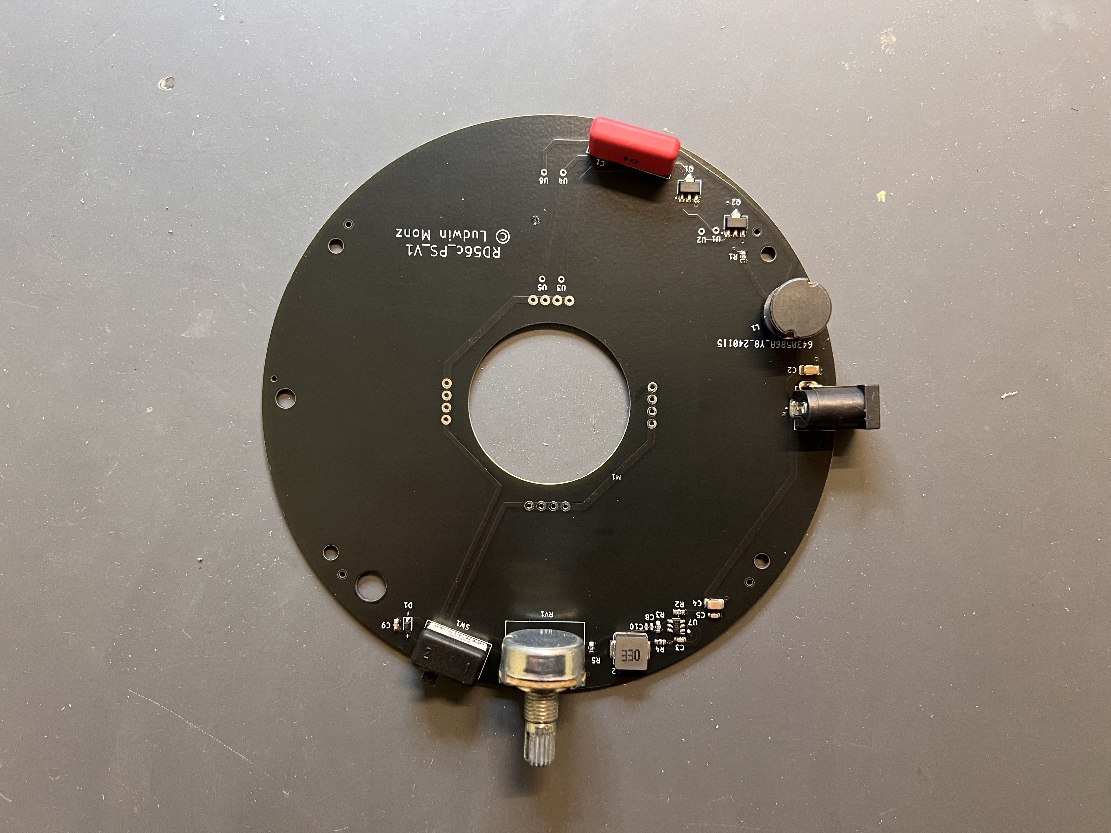
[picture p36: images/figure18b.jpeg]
  
</p>
<p align="center"> 
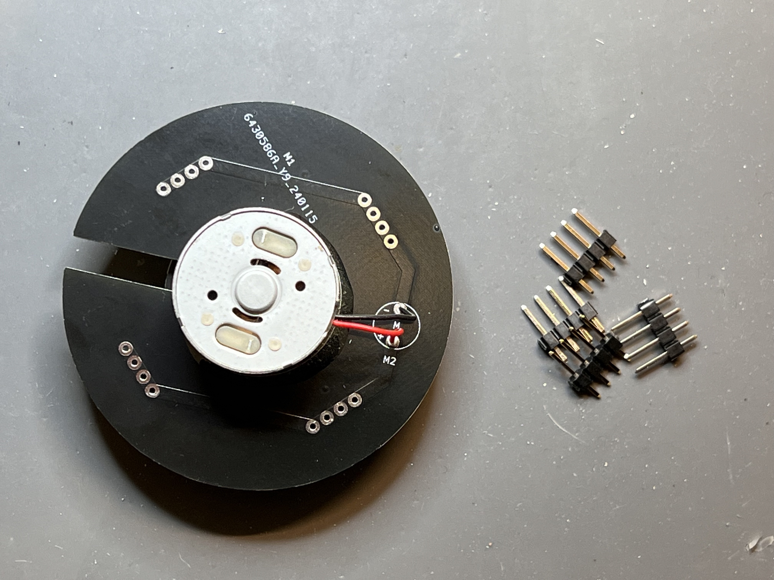
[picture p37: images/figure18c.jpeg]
  
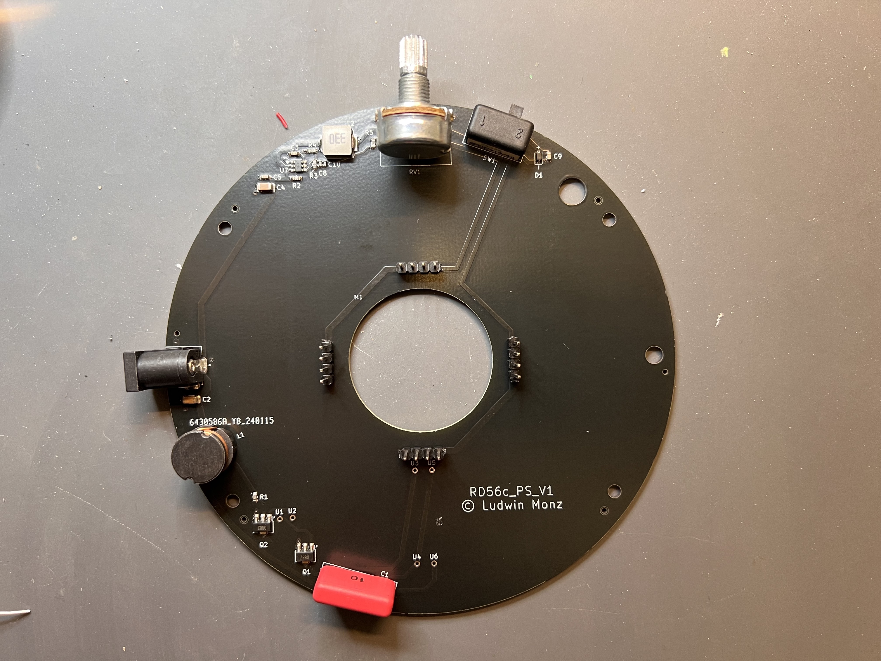
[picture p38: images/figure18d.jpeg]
  
</p>
<p align="center"> 
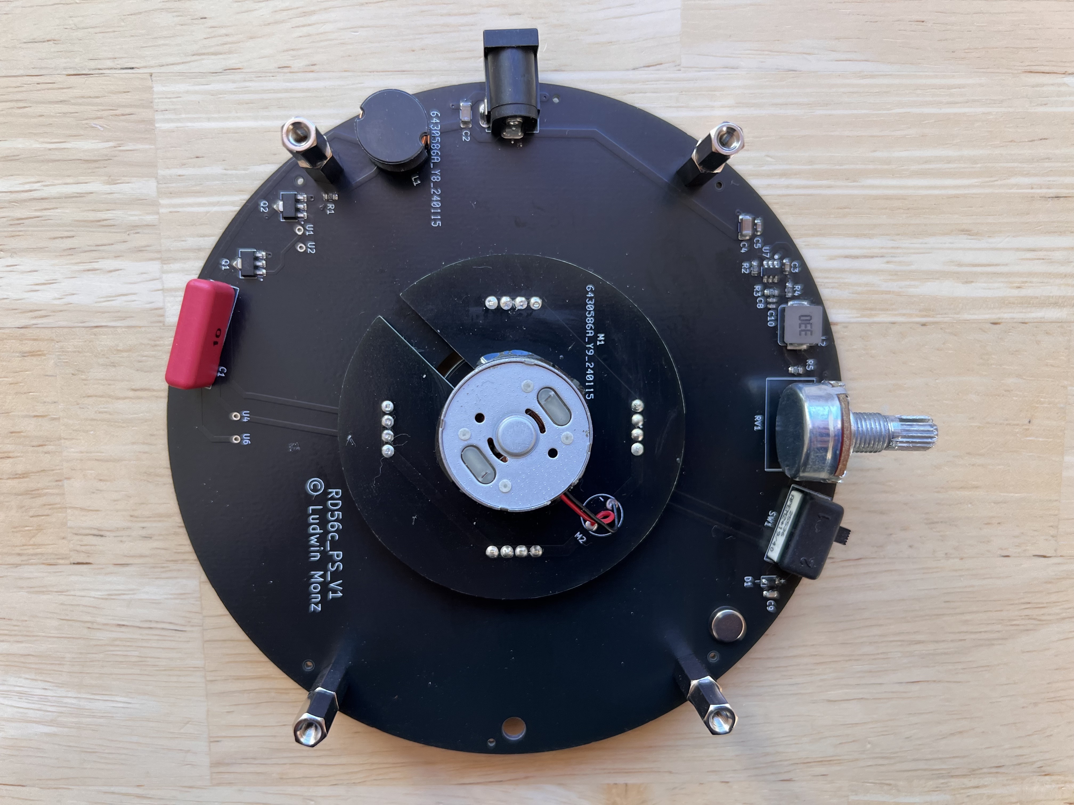
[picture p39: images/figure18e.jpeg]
  
</p>

**Figure 18:** Solder the through-hole components to the power supply board. Use 4-pin connectors to attach the motor assembly to the power supply pcb. Screw four 20 mm bolts to the pcb.

<p align="center"> 
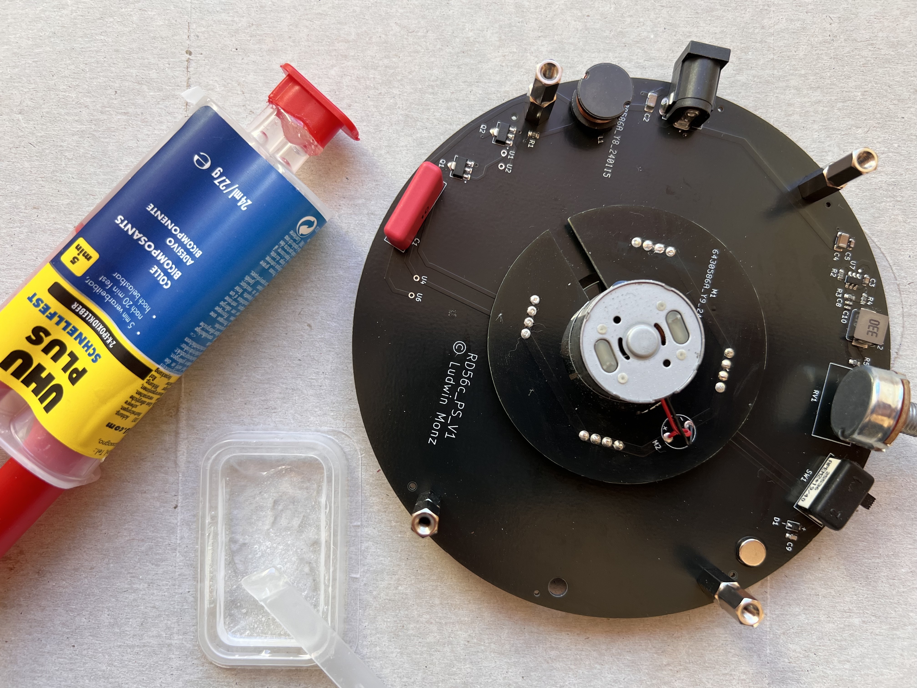
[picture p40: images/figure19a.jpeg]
  
  
</p>
<p align="center"> 
  
</p>

**Figure 19:** Glue rupper bumpers onto the bolts. Furthermore, glue the magnet into the respective hole in the power supply board. As the Hall sensor used can deal with any direction of the magnetic field, the orientation of the magnet does not matter.

<p align="center"> 
  
  
</p>

**Figure 20:** Use 6 pins to attach the secondary coil pcb to the back of the display board. Make sure, the two boards are connected and soldered tensionlessly, as the relative position between the two boards needs to be as precise as possible. Finally, use two M2 x 6 screws to attach the display pcb to the power supply assembly.

## 9. Conclusions

The rotating color display works according to a simple principle. However, the development of the Rotating Color Display device presented numerous highly interesting engineering challenges. Finding solutions for this was not only very interesting, but an opportunity to learn a wide variety of technologies. Last but not least, it was an intellectual challenge that I enjoyed a lot.

Worth mentioning are:

* Simple design with few mechanical components
* Replicable wireless power supply with printed coils
* interlacing for higher resolution and less flickering
* Complete balancing of the display board to ensure vibration-free operation
* Timer controlled clocking of the color LEDs and independent regulation of the R, G, and B brightness
* User-friendly user interface via a standard web browser
* Retrieval of time and weather data from the internet
* Display of animated GIF images
* Implementation of a file browser for the SD card for uploading image data
* Transparent, object-oriented structure of the ESP32 software

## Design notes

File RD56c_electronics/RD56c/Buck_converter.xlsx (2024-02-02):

V out | 5
V in(max) | 8
K ind | 0.3
I out | 1
f sw | 500000
L min (H) | 1.25e-05
L min (µH) | 12.5

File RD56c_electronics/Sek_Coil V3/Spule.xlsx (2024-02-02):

 | M | M | S | S | R | E | alpha | x | y
1 | 0 | 0.45 | 0 | 46 | 45.55 | -45.1 | 65 | 41.2823197 | 19.70026182
1 |  | -0.45 |  | -45.1 | -44.65 | 44.2
2 |  | 0.45 |  | 44.2 | 43.75 | -43.3
2 |  | -0.45 |  | -43.3 | -42.85 | 42.4
3 |  | 0.45 |  | 42.4 | 41.95 | -41.5
3 |  | -0.45 |  | -41.5 | -41.05 | 40.6
4 |  | 0.45 |  | 40.6 | 40.15 | -39.7
4 |  | -0.45 |  | -39.7 | -39.25 | 38.8
5 |  | 0.45 |  | 38.8 | 38.35 | -37.9
5 |  | -0.45 |  | -37.9 | -37.45 | 37
6 |  | 0.45 |  | 37 | 36.55 | -36.1
6 |  | -0.45 |  | -36.1 | -35.65 | 35.2
7 |  | 0.45 |  | 35.2 | 34.75 | -34.3
7 |  | -0.45 |  | -34.3 | -33.85 | 33.4
8 |  | 0.45 |  | 33.4 | 32.95 | -32.5
8 |  | -0.45 |  | -32.5 | -32.05 | 31.6
9 |  | 0.45 |  | 31.6 | 31.15 | -30.7
9 |  | -0.45 |  | -30.7 | -30.25 | 29.8
10 |  | 0.45 |  | 29.8 | 29.35 | -28.9
10 |  | -0.45 |  | -28.9 | -28.45 | 28
11 |  | 0.45 |  | 28 | 27.55 | -27.1
11 |  | -0.45 |  | -27.1 | -26.65 | 26.2
 |  | 0.45 |  | 26.2 | 25.75 | -25.3
 |  | -0.45 |  | -25.3 | -24.85 | 24.4
 |  | 0.45 |  | 24.4 | 23.95 | -23.5
 |  | -0.45 |  | -23.5 | -23.05 | 22.6
 |  | 0.45 |  | 22.6 | 22.15 | -21.7
 |  | -0.45 |  | -21.7 | -21.25 | 20.8

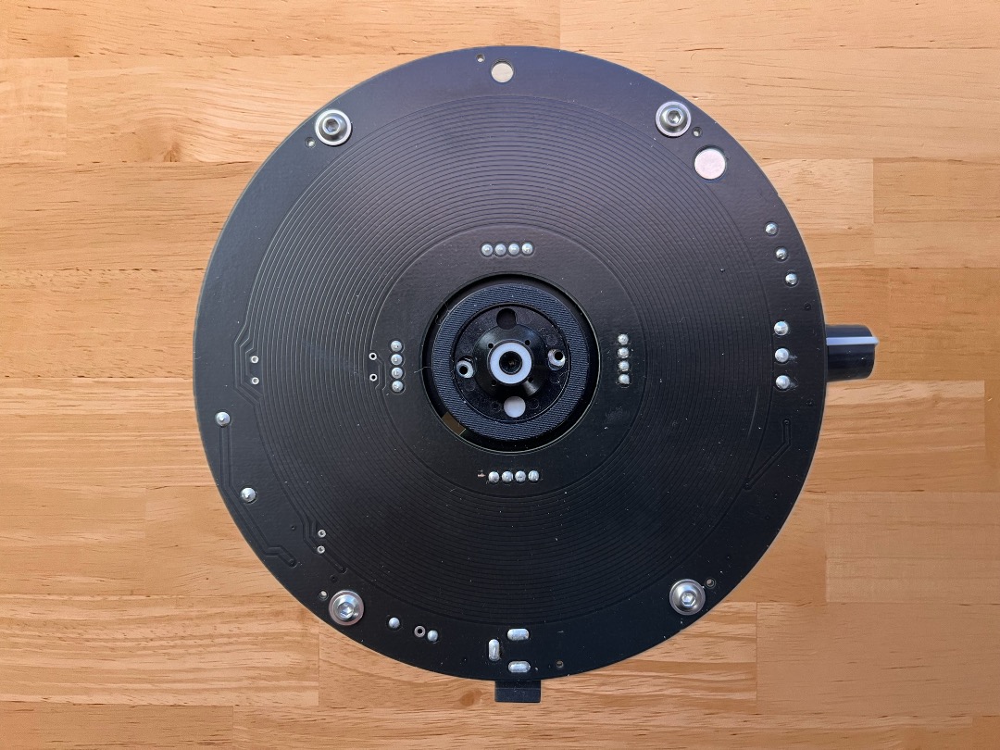
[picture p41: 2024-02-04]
images/figure06b2.jpg

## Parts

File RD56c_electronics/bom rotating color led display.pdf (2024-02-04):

## BOM Rotating Color LED Display

item # | Abbrev. | pieces | description | Source | Part Number | link | remark
1 | display pcb | 1 | RD56c printed circuit board fully assembled | JLCPCB | | https://jlcpcb.com | production files in repository: RD56c_electronics > RD56c > production > RD56_2023-12-24_21-22-23 (or newer)
2 | motor tray pcb | 1 | RD56c_motor_tray pcb. board only, no assembly | JLCPCB | | https://jlcpcb.com | production files in repository: RD56c_electronics > RD56c_motor_tray > production > RD56c_motor_tray_2024-01-14_13-01-49 (or newer)
3 | power supply pcb | 1 | RD56c_PS_V1 printed circuit board fully assembled | JLCPCB | | https://jlcpcb.com | production files in repository: RD56c_electronics > RD56c_PS_V1 > production > RD56c_PS_V1_2024-01-14_12-52-29 (or newer)
4 | secondary coil pcb | 1 | Sel_coil_V3 pcb. board only, no assembly | JLCPCB | | https://jlcpcb.com | production files in repository: RD56c_electronics > Sek_Coil V3 > production > Sek_Coil_V3_2023-12-24_21-47-37 (or newer)
5 | tray pcb | | tray pcb. board only, no assembly | JLCPCB | | https://jlcpcb.com | production files in repository: RD56c_electronics > tray > production > tray_2024-01-14_13-11-16 (or newer)
6 | J2 | 1 | CONN PWR JACK 2.1X5.5MM SOLDER | Digi-Key | EJ503A-ND | https://www.digikey.de/short/d4d54834
7 | RV1 | 1 | Potentiometer 100k linear | Digi-Key | P160KN-0QC15B100K | https://www.digikey.de/short/3tj072jm
8 | C1 | 1 | capacitor 33nF, MKP10, 630V | Reichelt | MKP10-630 33N | https://www.reichelt.de/mkp10-pp-puls-kondensator-33-nf-10-630-vdc-rm-15-mkp10-630-33n-p31975.html?&nbc=1 | critical component! do NOT change type!!
9 | L1 | 1 | Coil 330 uH | Reichelt | L-09HVP 330µ | https://www.reichelt.de/stehende-induktivitaet-
09hvp-ferrit-330-h-l-09hvp-330--p255620.html?&nbc=1
10 | M1 | 1 | CD motor with tray | Amazon, ebay | RF-300F-12350
11 | magnet | 1 | magnet, diameter 6mm, thickness 3 mm | Amazon | Multi-Use Neodym Magnete - 6 x 3 mm | https://www.amazon.de/UTOMAG-Multi-Use-Neodym-Magnete-Aufbewahrungs/dp/B08F7HNG45/ref=sr_1_5?ke

ywords=neodym+magnete+6mm&qid=1659078 103&sr=8-5
12 | screw | 2 | M2x6 screw | generic
13 | M2 nuts | 2 | M2 nuts | generic
14 | M3 nuts | 3 | M3 nuts | generic
15 | bolt | 4 | bolt M3x20mm, female - female | Der Schraubenladen | Abstandsbolzen Messing vernickelt | https://shop.der-schraubenladen.de/schrauben/abstandsbolzen/1628/abstandsbolzen/distanzhalter-distin-innen/innen-messing-vernickelt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
16 | screw | 7 | screw flat head, M3x6 | Der Schraubenladen | ISO 7380-2 Linsenschraube mit Flansch Innensechskant Edelstahl A2 | https://shop.der-schraubenladen.de/schrauben/metrische-schrauben/schrauben-flachkopf/2144/iso-7380-

2-linsenschraube-mit-flansch-innensechskantedelstahl-a2?number=SW12060.28&c=10
17 | bumper | 4 | bumper lens shape, diam. 6.4 mm, thickness 1.9 mm | Amazon | Home Xpert 70 Stück Schutzpuffer CLEAR Linse | https://amzn.eu/d/7VAHGcK
18 | pins 2,54 mm | 1 | 2.54 mm pin row | Reichelt | SL 1X50G 2,54 | https://www.reichelt.de/50pol-stiftleiste-gerade-rm-2-54-sl-1x50g-2-54-p19508.html?&nbc=1
19 | sw1a | 1 | switch, 90 degree, pcb mount

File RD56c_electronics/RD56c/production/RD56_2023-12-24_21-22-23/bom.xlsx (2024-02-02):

Designator | Footprint | Quantity | Value | LCSC Part #
C201, C203, C210, C212, C301, C304, C308, C309, C312, C315, C316, C318, C401, C402, C403, C404, C405, C406, C407, C408, C409, C410, C416, C417, C501, C503, C505, C601, C603, C701, C703 | 0402 | 31 | 100nF | C307331
C202, C211 | 1206 | 2 | 10µF, 50V | C13585
C204, C205, C213, C214 | 1206 | 4 | 22µF, 25V | C12891
C206, C216 | 0402 | 2 | 47pF | C1567
C207, C208 | 0805 | 2 | 22µF, 25V | C45783
C209, C313, C314 | 0402 | 3 | 10pF | C32949
C215 | 0603 | 1 | 30pF | C1658
C302 | 0402 | 1 | 10nF | C15195
C303, C305, C310, C317, C412, C413 | 0402 | 6 | 1µF | C52923
C306, C307 | 0402 | 2 | 3p3 | C1565
C311, C319, C502, C504, C506, C602, C604, C702, C704, C801, C802, C803, C804, C805, C806, C807, C808, C809, C810, C811, C812, C813, C814, C815, C816, C817, C818, C819, C820, C821, C822, C823, C824, C825, C826, C827, C828, C901, C902, C903, C904, C905, C906, C907, C908, C909, C910, C911, C912, C913, C914, C915, C916, C917, C918, C919, C920, C921, C922, C923, C924, C925, C926, C927, C928 | 0603 | 65 | 10µF | C96446
C411 | 0805 | 1 | 10µF | C15850
C414, C415 | 0402 | 2 | 27pF | C1557
D201, D202, D203, D204 | DIOM7959X265N | 4 | SS34 | C8678
D801, D802, D803, D804, D805, D806, D807, D808, D809, D810, D811, D812, D813, D814, D815, D816, D817, D818, D819, D820, D821, D822, D823, D824, D825, D826, D827, D828, D901, D902, D903, D904, D905, D906, D907, D908, D909, D910, D911, D912, D913, D914, D915, D916, D917, D918, D919, D920, D921, D922, D923, D924, D925, D926, D927, D928 | LED_RGB_1210 | 56 | LED_BARG | C513366
J301 | microSD_SMD | 1 | Micro_SD_Card | C5155564
J302, J401 | USB_C_Receptacle | 2 | USB_C_Receptacle_USB2.0 | C709357
L201, L203 | L_Bourns_SRP7028A_7.3x6.6mm | 2 | 33µH | C177245
L301, L302 | 0402 | 2 | 2n2 | C412264
R201, R202, R204, R205, R303 | 0402 | 5 | 100k | C25741
R203 | 0402 | 1 | 22k | C25768
R206 | 0603 | 1 | 13k | C22797
R301, R304, R310, R403, R501, R508 | 0402 | 6 | 10k | C25744
R302 | 0402 | 1 | 22 | C25092
R305, R306, R307, R308, R309 | 0402 | 5 | 0 | C17168
R311, R312, R401, R402 | 0402 | 4 | 5k1 | C25905
R404, R405 | 0402 | 2 | 27R | C321419
R406, R407, R502, R503, R504, R505, R506, R507, R509, R510, R511, R601, R602, R603, R604, R605, R606, R701, R702, R703, R704, R705, R706 | 0402 | 23 | 1k | C11702
R409 | 0402 | 1 | 20k | C25765
SW301 | ROCPU_switch | 1 | boot | C5381238
SW302, SW401 | ROCPU_switch | 2 | reset | C5381238
SW402 | ROCPU_switch | 1 | USB boot | C5381238
U201, U202 | SOT-23-6 | 2 | TPS54202DDC | C191884
U302 | IC_ESP32-S3 | 1 | ESP32-S3 | C2913192
U303, U404 | SOIC-8_5.23x5.23mm_P1.27mm | 2 | W25Q128JVS | C97521
U304, U401 | SOT-23-6 | 2 | USBLC6-2SC6 | C2687116
U402 | QFN-56-1EP_7x7mm_P0.4mm_EP3.2x3.2mm | 1 | RP2040 | C2040
U403 | MH253 | 1 | MH253 | C114369
U501, U502, U503, U601, U602, U701, U702 | TQFP48-EP_STM | 7 | STP24DP05BTR | C157417
Y301 | Crystal_SMD_4Pin_3.2x2.5mm | 1 | 40 MHz | C379787
Y401 | Crystal_SMD_3225-4Pin_3.2x2.5mm | 1 | 12MHz | C9002

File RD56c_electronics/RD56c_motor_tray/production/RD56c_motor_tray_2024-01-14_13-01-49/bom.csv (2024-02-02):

Designator | Footprint | Quantity | Value | LCSC Part #
M1 | motor_tray | 1 | Motor_DC
M2 | motor | 1 | Motor_DC

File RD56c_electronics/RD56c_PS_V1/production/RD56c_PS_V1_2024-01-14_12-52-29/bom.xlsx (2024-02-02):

Designator | Footprint | Quantity | Value | LCSC Part #
C10 | 0402 | 1 | 10pF | C32949
C2 | 1206 | 1 | 10µ, 50V | C13585
C3, C5, C9 | 0603 | 3 | 100nF | C14663
C4 | 1206 | 1 | 10µF, 50V | C13585
C6, C7 | 0805 | 2 | 22µF, 25V | C45783
C8 | 0402 | 1 | 47pF | C1567
D1 | 1N5819 | 1 | 1N5819 | C191023
L2 | L_Bourns_SRP7028A_7.3x6.6mm | 1 | 33µH | C177245
Q1, Q2 | D882 | 2 | D882 | C9634
R1 | 0603 | 1 | 2k2 | C4190
R2, R3 | 0603 | 2 | 100k | C25803
R4 | 0603 | 1 | 120k | C25808
R5 | 0603 | 1 | 12k | C22790
U7 | SOT-23-6 | 1 | TPS54202DDC | C191884

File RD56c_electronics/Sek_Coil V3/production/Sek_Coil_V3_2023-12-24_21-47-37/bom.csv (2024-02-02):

Designator | Footprint | Quantity | Value | LCSC Part #
L101 | coil_large | 1 | ~

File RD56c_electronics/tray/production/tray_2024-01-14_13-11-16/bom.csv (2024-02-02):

Designator | Footprint | Quantity | Value | LCSC Part #
R0 | R_Axial_DIN0204_L3.6mm_D1.6mm_P5.08mm_Horizontal | 1

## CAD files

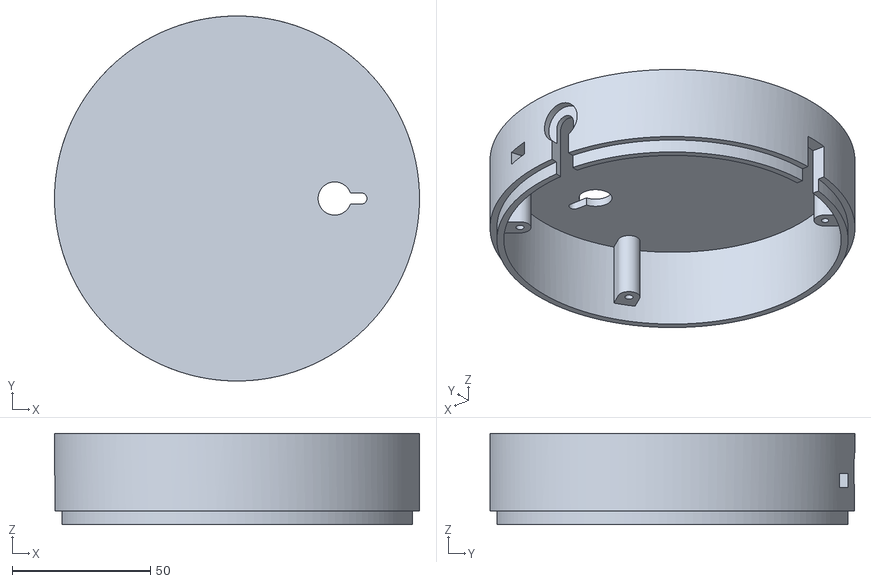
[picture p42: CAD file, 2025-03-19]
RD56c_case_by galmiklos/RD56c-CaseBottom.stl
132.0 x 132.0 x 33.0

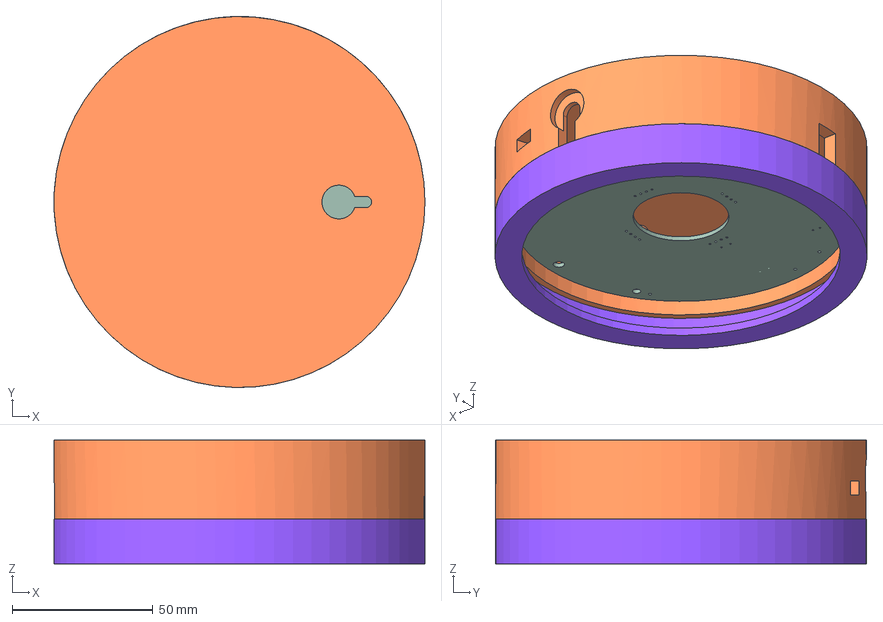
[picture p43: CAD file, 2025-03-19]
RD56c_case_by galmiklos/RD56c-Case.FCStd
132.0 x 132.0 x 44.0 mm
CaseBottom
CQ assembly
CQ assembly001
CQ assembly002
CQ assembly003
CQ assembly004
C_1206_3216Metric
R_0603_1608Metric
R_0603_1608Metric002
CQ assembly006
CQ assembly007
CQ assembly008
CQ assembly009
CQ assembly010
D_SOD_323F
C_0603_1608Metric
R_0603_1608Metric004
C_1206_3216Metric002
C_0603_1608Metric002
C_0805_2012Metric
R_0603_1608Metric006
C_0402_1005Metric
R_0603_1608Metric008
C_0805_2012Metric002
SOT_23_6
C_0603_1608Metric004
C_0402_1005Metric002
RD56c_PS_V1_PCB
CaseTop

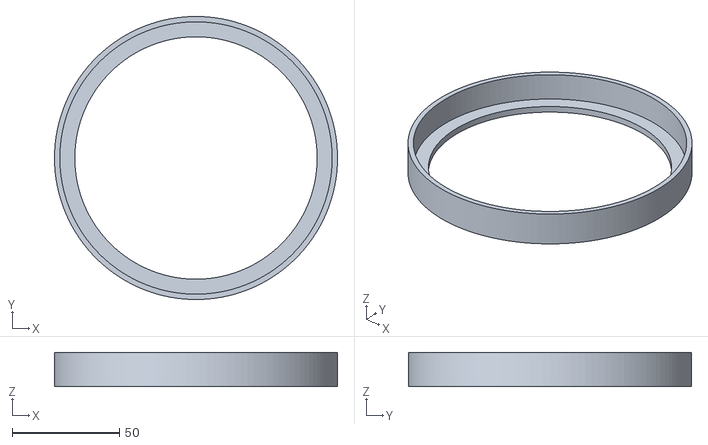
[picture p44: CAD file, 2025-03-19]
RD56c_case_by galmiklos/RD56c-CaseTop.stl
132.0 x 132.0 x 16.0

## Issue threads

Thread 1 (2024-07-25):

Switch type number

HubSteven, 2024-07-25:
What is the type of switch you used on the power supply board for SW1A? It's not listed in the bom.

lhm0, 2024-07-25:
I bought this switch in Germany:

https://www.reichelt.de/schiebeschalter-90-rm5-08-1x-ein-ein-ss-25536-n-p105721.html?&nbc=1#

There is a data sheet on their page.

The manufacturer is APEM, type SS 25536 N

The component is also available on mouser.com .

HubSteven, 2024-07-26:
Thank you!

Closed 2024-07-26.

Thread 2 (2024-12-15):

"Failed to open file for reading"

HubSteven, 2024-12-15:
Hi,
I've flashed both the ESP32 and the Raspberry Pi Pico on the pcb.
The micro SD card also has the necessary files in the root directory.
However the LED's won't light up and I don't get any webpage when I'm connected to the SSID.
The ESP32 show's the following in the terminal connection over  USB:

> start initialization....
SD Card Type: SDSC
SD Card Size: 121MB
nun folgt .read_f()
Failed to open file for reading
.read_f() abgeschlossen
Failed to open file for reading
Access Point started.
IP-Adresse: 192.168.4.1
Failed to open file for reading
SD Card Type: SDSC
SD Card Size: 121MB
der Server wurde gestartet
Zeit: 1:0:2
request weather data.....
Wifi connection lost...
ERROR:
deserializeJson() failed: EmptyInput
icon: 0
temp: 0.0 C
humidity: null %
Failed to open file for reading
Failed to open file for reading
Failed to open file for reading
Failed to open file for reading
Failed to open file for reading
Failed to open file for reading
Failed to open file for reading
Failed to open file for reading
Failed to open file for reading
Failed to open file for reading
Failed to open file for reading

I've tried several microSD cards with different sizes.

lhm0, 2024-12-15:
Hi Hub,

from the serial output we can read, that

1. the ESP32 microcontroller is running. That is good news.
2. there should be a Wifi access point ("RD56c"). If you can connect to this AP (even without any response from the server) is another good sign. It means, that the WiFi function is working as well.
3. the microcontroller can talk to the SD card. Otherwise, the output would be "card mount failed". But you get "SD Card Type: SDSC, SD Card Size: 121MB". This means, card mount was successful. Good news.

Given 3, it sounds like the software does not find the files it is looking for. Let's check the file structure:

the folders "gif", "html", "images", and "variables" all need to be in the root directory. For the initialization the "variables" folder needs to have the various *.txt" files, as you can see from the "data" folder of the repository.

It really looks like the ESP32 is very close to full function.

I am more concerned about the RP2040, as you do not see any flickering of the LEDs. This seems to indicate, that the RP2040 is not running. Did the software upload work for the RP2040? Are there any messages on the serial port?

Best regards,

Ludwin

lhm0, 2024-12-15:
another thought if the file structure of the SD card is correct: what format does the SD card have? You need to use FAT32.

I had some trouble in the past with formatting the SD card under Windows. If problems persist, you might want to re-format the card with https://www.sdcard.org/downloads/formatter/ . This program works for sure.

lhm0, 2024-12-15:
I check on the RP2040: there should be a message "brightness: 0" once every second on the USB port.

If you use the Visual Studio Code terminal for monitoring, it might be tricky to connect to the microcontroller.

HubSteven, 2024-12-15:
Thanks for your quick reply. I do indeed have the "brightness: 0"message from the RP2040.
My directory structure on the SD card look like this:
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

HubSteven, 2024-12-15:
Also tried the sd card formatter tool, but still the same thing.
I don't have the DC motor yet so the rd56c pcb is on top of the PS  PCB with a piece of paper in between to prevent shorts.
Without the PCB rotating and without SD card, the LED's should still light up for a test pattern?

lhm0, 2024-12-15:
yes, even without rotation there should be a flickering. Also, it does not matter, what the ESP32 is doing. The SD card is irrelevant for the flickering.

Let me look into the SD card issue. Very, very strange

HubSteven, 2024-12-15:
My 5V supply is dead, got some hardware fixing to do. I'll let you know once it works.
BTW I've noticed that on the silkscreen C310 and C311 are swapped.
Another thing to take into account is that the DC motor apparently has two versions. I've orderd the wrong one.
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
This one has the same type number but a different piece of plastic with 3 screw holes instead of four.

lhm0, 2024-12-15:
ok. That explains, why you do not see any flickering.

regarding the motor, there are several versions, unfortunately. The one that you have might still work, as long as the height of the assembly is the same.

lhm0, 2024-12-15:
I have added a test program for the SD card reader. Please check the subfolder "RD56c_ESP32_SD_Test" of the repository and upload to the ESP32.

The software should list all files of the SD card via the Serial monitor.

HubSteven, 2024-12-15:
Just fixed the sort on the 5V line, the LEDs light up now (red and blue flickering).
From your sd test code I get this:
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

lhm0, 2024-12-15:
there were a couple of inconsistencies, which I have corrected. Please download the latest repository and upload the code to the ESP32. I hope things will work, now.

Great to hear, that you have fixed the 5V supply. There should be a "red-green-blue" sequence with different phases on the left and the right half of the LED row.

If the ESP32 works correctly, the "red-green-blue" sequence should be replaced with some white flickering after 10 seconds, or so.

Try out the web interface. It should work, now.

Keep me posted. I will check tomorrow.

HubSteven, 2024-12-15:
Great, it finally works! I'll keep this issue opened to post you a picture of the whole assembly once I've got the DC motor in.

lhm0, 2024-12-17:
Dear Hub, I spent an afternoon on bug fixing the software. The file browser is much more stable now, though still not 100% perfect. But it is usable. Furthermore, I have added a new start screen background with a "real gear".
As you might know, I have been working on a single microcontroller display (monochrome) for a while. However, in comparison, the image stability of the color display is so much better. There is no jitter, no instability. The dual controller approach might have its disadvantages, but the performance is simply a different class.

HubSteven, 2024-12-17:
Thank you, got it uploaded to the ESP32. I'll let you know once I got the motor in.

HubSteven, 2025-01-19:
I got the cd motor in. I was only wondering if the slit of the pcb with the two m2 nuts should be inserted over the indicated piece of plastic. Because it seems to be too thick to fit in the slit of the pcb.

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

lhm0, 2025-01-19:
here is how it looks with my motor:

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

galmiklos, 2025-01-22:
Hi Steven,
Sorry for contacting you here, I couldn't find a way to private message you. I am thinking about building it, too, and was trying to find PCBs, so I reached out to Ludwin in the comments section on youtube, and he pointed out that you are in the middle of building, and that you may have an extra set available. I know when ordering, the minimum number is usually 5, so before I spend $80 to order 5 sets, I was hoping to find someone with surplus boards. If you can spare a set or two, it could also lower your cost overall, I'm willing to "chip in".From your profile and the discussion I couldn't tell where you were located, hopefully on this side of the pond, so that shipping would not be too expensive. I live in Texas. You can email me directly at miklos.gal@gmail.com, too.
Thanks,
MIki.

HubSteven, 2025-01-23:
@galmiklos I'm located in the Netherlands, so I don't think sending you my PCBs will make it any cheaper for you. Besides I've hand soldered every SMD component, that's something I would not recommend. Getting them pre-assembled is much easier.

@lhm0 I've put together the whole assembly and it fully works, only got some problems with balancing so it sound a bit like an old Diesel right now haha.

Only problem I have is with changing the animation logo's. Is this what the webpage should look like?

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

lhm0, 2025-01-23:
now I am really impressed: you hand soldered this PCB? You must be an artist.

Yes, this is the right screen for the data conversion. You can convert any image (including GIFs).

1. Tap on "load image". A file selection box will come up, which allows you to select and load an image from your mobile phone to the display.
2. The upper file selection box should show the contents of your SD card. I am not sure why it does not do so, in your screen shot. Maneuver to a folder, where you would like to store the converted image.
3. you can either scale or crop the image. Tap "save .rdc". Now, the controller will save the image to the SD card. Please note: it will take quite a while until this process is completed. Depending on the image size it can easily take a minute or more.
4. now you need to assign the file to either the clock or the image mode. long-tap on the filename in the upper selection box, then tap on "select logo" or "select image".

galmiklos, 2025-01-24:
@HubSteven , yes, that's what I do too, hand solder the components. I usually make my own PCBs, including solder mask and silk screen, but I only can do double sided. But yes, shipping from the Netherlands is not an option. Thanks for taking the time to answer.

Closed 2025-02-27.

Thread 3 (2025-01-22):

Drawing sheet empty_sheet.kicad_wks not found

galmiklos, 2025-01-22:
I know, it's just cosmetics, but if by any chance empty_sheet.kicad_wks could be added to the repository, KiCAD could look a little prettier, I suppose. Obviously, I don't have that path (C:/Users/lbmon/Dropbox/Ludwin/Elektronik/KICAD/Projekte/empty_sheet.kicad_wks), but one could select the file in the page settings.

Thanks!

lhm0, 2025-01-22:
Hi Miklas,

no problem. I have added the file to the repository and changed the setting in the KiCAD files. The PCBs should open without error message, now.

However, you might notice that the board is not centered to the drawing sheet but sits centered to the top left corner of the page. For some reason, KiCAD uses this corner as the center of its coordinate system. As almost all coordinates of components and even traces in my PCBs are computed, I tried to make my life somewhat easier. If you can figure out a way to move the center of the coordinate system to the center of the page, please let me know.

It's cosmetics, but I would like to further improve it.

lhm0, 2025-01-24:
Thank you for the link. I will use it for future projects.

Best regards, Ludwin

Closed 2025-01-24.

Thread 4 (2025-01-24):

Building questions - Miklos Gal

galmiklos, 2025-01-24:
I hope it's OK I started a new "issue" thread, similar to the one @HubSteven started, to partly document my progress, but mostly to post my questions. I wanted to avoid getting confused who asked what.

So, here's my first question.

I placed an order for the parts at LCSC, it was super helpful to have all those up-to-date LCSC part numbers in the BOMs. Thank you Ludwin!

I am about to place the order for the PCBs, and I wasn't sure how important it is to have the top board black. I think other colors would see through, and it was not a coincidence we see black PCBs on the pictures.

Thanks,
Miki.

lhm0, 2025-01-24:
Hi Miklos, the new "issue" thread is perfectly fine.

When I ordered my assembled PCBs from JLCPCB, there was no need to order the parts separately. I just uploaded the PCB data, the BOM and the position file. They directly quoted the PCBs, including the parts.

Anyhow, I assume it will not hurt to order the parts separately.

Regarding the PCB color, I only noticed later that they charge extra for black. I did order green boards in the past, but only for my monochrome displays. The reason for black is that I wanted a higher contrast. I am sure you will also get a nice image with a green PCB, but the contrast will be somewhat lower, when there is some ambient light. But again, I do not have the comparison, unfortunately.

galmiklos, 2025-02-02:
A quick update. The PCBs just shipped, and I went for the black board for the display (the one with the LEDs). I also ordered the stencil for the display board (for $7). I never had a professionally made stencil, always used hand made ones (thin plastic sheets cut with an Acto knife). A little bit of luxury... ;-). For good measure, I "upgraded" my faithful $60 heatgun to a Quick 861DW. :-) It's my birthday!

I also started experimenting with an inventory software I stumbled upon (well I was searching for one), it's InvenTree. Opensource, and looks great.

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

Not sure if you use any inventory software, if you want to give it a try, it's not that hard to install it, although not the simplest. I am just showing the "build" section above, that would be the completion of the journey, eventually resulting a sellable part (not that I have any intention to sell), and removing all the used parts from the inventory.

lhm0, 2025-02-02:
Hi Miklos,

Thanks for the update. Let me know when the boards arrive. I am curious whether you like the quality. Will you assemble the power supply board yourself?

No, I do not use an inventory software yet - maybe a future project.

galmiklos, 2025-02-05:
Holly cow! I am about to receive the boards, but UPS sent me an e-mail, that I have to pay to the driver. What!???

Turns out, I have to pay customs, which sounds fair, but UPS makes me pay "brokerage charges". And that is an outrageous amount! The boards cost me $65, shipping $37, sales tax $8 (I'm rounding). Customs is $8, and the brokerage charges are $60!!! :-(

I have to figure out how I can avoid this in the future. It is something with what shipping method you chose, I didn't have to pay anything when other small boards were shipped cheap. But for this larger shipment, JLCPCB only had expensive shipping methods, like UPS.

galmiklos, 2025-02-05:
Well, it looks like it was an expensive stencil after all...

The whole order, without stencil would have been $95.23, including shipping, tax and customs.

But because of the $7 stencil, cheap shipping was not available, and I think I know why. I just got the stencil (as a separate box), and it is pretty large. I mean it's not thick, but about as big as an A3 sheet. So, the shipping became more expensive, and customs was not included, but left to UPS to handle it. And the way UPS handles it is that they hire 3rd party brokers to handle customs, and these brokers cost an arm and a leg!

My total is now $179.03 ($111.78 as the order itself, plus $67.25 for customs and brokerage fee).

So, that stencil cost me $83.8! :-(

galmiklos, 2025-02-06:
As Borat once said: "Very Nice!" :-)

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

And I like the quality!

And yes, I wanted to build everything, including the power supply. Should I be worried about your question? Does it mean you think it will be challenging?

lhm0, 2025-02-07:
The UPS charges are really annoying. I also like to use UPS, but have never had such an experience.

Unfortunately, I have no experience with self-assembling the pcb. I have too much respect for the small pitch of the microcontrollers. I'm keeping my fingers crossed that it works.

When populating the board, please note the finding of @HubSteven: "BTW I've noticed that on the silkscreen C310 and C311 are swapped."

I corrected the silkscreen, but I don't know which version of the pcb you have.

galmiklos, 2025-02-10:
Yes, I can see in KiCad PCB Editor, that C310 and C311 are labeled correctly, however, I was lazy enough to use the already prepared production zip files, and I can see on the board that indeed, the two capacitors are swapped. Of course, it's hard to miss, when you try to solder a 0402 capacitor on a 0603 pad, and vice versa... ;-)

My laziness also led to another fiasco, although it is just delay (for now). I ordered the parts from LCSC, as those part numbers were already in the BOMs, and also, I took it for granted, that parts from China will be cheaper. Well, I probably wouldn't have paid too much more, if at all, if I ordered everything from digikey. Although, for some reason I cannot explain, I got a pretty good discount. :-)

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

And even with the cheapest shipping, it wouldn't take more than a week to get the parts from digikey. The parts from LCSC have been "in transit" for almost two weeks, and the shipment is still at the Hong Kong airport. :-(

I can't wait to receive the parts, so that I can start building!

galmiklos, 2025-02-10:
I was bitching about the ~$180 total cost of the boards (because of outrageous shipping costs), so I started looking for a US based company. Well, only the RD56 board costs more...

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

And it's only 3 boards not 5, and tax and shipping is not yet included. I guess I'm still OK. :-)

lhm0, 2025-02-11:
I agree, despite of all the charges JLCPCB is still a good deal.

I have never bought directly from LCSC. JLCPCB uses them as their main supplier and they use the same part numbers. This is the reason why I have these numbers in the BOM. You can check JLCPCB's inventory under jlcpcb.com/parts . I picked parts that JLCPCB had on stock. JLCPCB seems to get high discounts from LCSC. Their component prices are far below, what I would get from local sources here in Germany.

Anyhow, I hope that your parcel finally arrives. Good luck with soldering.

galmiklos, 2025-02-12:
Yes, finally it started moving, it is at the "local distributor" now in Los Angeles. :-)

In the meanwhile I realized another flaw in my ordering process, namely, that I ordered the exact number of integrated circuits needed. Why do I think I won't blow up a few? ;-) So, I quickly ordered some extra from Mouser, since I anyway had to order that "critical" capacitor from them (didn't want to order from Germany, that would have cost me an arm and a leg).

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

I noticed something, though. Although I searched for RP2040, I found this part, which I ordered.

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

Does it look like the correct one to you? It's a different manufacturer part number from LCSCs one: SC0914(13).

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

lhm0, 2025-02-14:
The RP2040 looks good to me.

I hope you will not blow up any components. I used to have some issues with the two transistors on the power supply board. The current can be pretty high depending on the load applied by the display. But after I had replaced the transistors with the current model, that issue was entirely gone.

Have fun with the assembly!

lhm0, 2025-02-14:
I looked up what I payed for the display board. Here is the invoice (it was ordered pretty exactly 1 year ago)

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

The assembly includes all components. I got 3 assembled boards and 2 bare pcbs.

galmiklos, 2025-02-16:
I may not have used the right word, it's not "blowing up" I'm worried about, but "cooking", really. The other day I tried out my new hot air station, and after soldering in the integrated circuit, the device didn't work. I replaced the part by soldering it manually, and the device started working. So, I think I cooked that part with my hot air station. I have to practice, there is no way of hand soldering the ESP and RP chips.

@HubSteven, at what temperature did you have your hot air set when soldering your QFNs?

galmiklos, 2025-02-17:
I am trying to compile the ESP firmware, but it fails with the below messages.
```

Processing um_pros3 (platform: espressif32; board: um_pros3; framework: arduino)
----------------------------------------------------------------------------------------------------------------------------------------------------------------------------
Verbose mode can be enabled via `-v, --verbose` option
CONFIGURATION: https://docs.platformio.org/page/boards/espressif32/um_pros3.html
PLATFORM: Espressif 32 (5.4.0) > Unexpected Maker PROS3
HARDWARE: ESP32S3 240MHz, 320KB RAM, 16MB Flash
DEBUG: Current (cmsis-dap) External (cmsis-dap, esp-bridge, esp-builtin, esp-prog, iot-bus-jtag, jlink, minimodule, olimex-arm-usb-ocd, olimex-arm-usb-ocd-h, olimex-arm-usb-tiny-h, olimex-jtag-tiny, tumpa)
PACKAGES:
 - framework-arduinoespressif32 @ 3.20006.221224 (2.0.6)
 - tool-esptoolpy @ 1.40400.0 (4.4.0)
 - tool-openocd-esp32 @ 2.1100.20220706 (11.0)
 - toolchain-riscv32-esp @ 8.4.0+2021r2-patch5
 - toolchain-xtensa-esp32s3 @ 8.4.0+2021r2-patch5
LDF: Library Dependency Finder -> https://bit.ly/configure-pio-ldf
LDF Modes: Finder ~ deep, Compatibility ~ soft
Found 39 compatible libraries
Scanning dependencies...
Dependency Graph
|-- ESPAsyncTCP @ 2.0.0
|-- ESPAsyncWebServer @ 3.6.0+sha.ad3741d
|-- Time @ 1.6.1+sha.a18e50d
|-- ESP32DMASPI @ 0.3.0
|-- ArduinoJson @ 7.3.0
|-- FS @ 2.0.0
|-- SD @ 2.0.0
|-- SPI @ 2.0.0
|-- WiFi @ 2.0.0
|-- HTTPClient @ 2.0.0
|-- WebServer @ 2.0.0
|-- ESPmDNS @ 2.0.0
Building in release mode
Compiling .pio/build/um_pros3/src/my_ESP.cpp.o
Compiling .pio/build/um_pros3/libbf3/ESPAsyncTCP/AsyncPrinter.cpp.o
Compiling .pio/build/um_pros3/libbf3/ESPAsyncTCP/ESPAsyncTCP.cpp.o
Compiling .pio/build/um_pros3/libbf3/ESPAsyncTCP/ESPAsyncTCPbuffer.cpp.o
Compiling .pio/build/um_pros3/libbf3/ESPAsyncTCP/SyncClient.cpp.o
Archiving .pio/build/um_pros3/lib326/libAsyncTCP.a
.pio/libdeps/um_pros3/ESPAsyncTCP/src/ESPAsyncTCPbuffer.cpp:27:10: fatal error: debug.h: No such file or directory

***************************************************************
* Looking for debug.h dependency? Check our library registry!
*
* CLI  > platformio lib search "header:debug.h"
* Web  > https://registry.platformio.org/search?q=header:debug.h
*
***************************************************************

 #include <debug.h>
          ^~~~~~~~~
compilation terminated.
Indexing .pio/build/um_pros3/lib326/libAsyncTCP.a
.pio/libdeps/um_pros3/ESPAsyncTCP/src/SyncClient.cpp:25:10: fatal error: interrupts.h: No such file or directory

********************************************************************
* Looking for interrupts.h dependency? Check our library registry!
*
* CLI  > platformio lib search "header:interrupts.h"
* Web  > https://registry.platformio.org/search?q=header:interrupts.h
*
********************************************************************
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

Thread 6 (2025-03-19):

Missing Libraries

kelbycriswell, 2025-03-19:
Cloned to local and when attempting to compile it throws a lot of missing reference errors, could you include all library files in a component folder or such. I was trying to compile the esp32 version.

lhm0, 2025-03-19:
The software package is designed for platformIO. Please note the platformio.ini file. It lists all libraries necessary. PlatformIO loads these libraries automatically - no need to install manually.

If you are using platformIO, please post the error message.

galmiklos, 2025-03-19:
@kelbycriswell , are you by chance in the US? Have you already ordered your PCBs? I have a few extra sets (all boards), we could make a deal to save you a few dollars, and help me recover some of my PCB cost.

kelbycriswell, 2025-03-20:
I am in the states. I have a chinese model that  uses just an esp32-s and
it worked fine until the mcu died. So I was going to get a build working
then see if I could tweek it since it appears your design relies on a
rp2040 as the mcu and the esp32 as the wifi correct? Or did I misinterpret
the schematics? I usually order my PCBs from PCBway, but the tariffs  are
going to mess that up

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

galmiklos, 2025-03-20:
@kelbycriswell, it is not my design, Ludwig (@lhm0) designed it, I'm just an enthusiastic builder. In my case it was not the tariffs that increased the cost, but UPS's "broker fees". It came to a hefty $67, on top of shipping and JLCPCB's price. Overall, 5 sets of boards cost me about $180. So, if you want a set, you can have it for $36 plus shipping. If you are not interested in building it, just want to play with it, I have one extra device built, you can have that, too, but I would have to calculate how much the parts cost. I wouldn't want to make any profit, as I said it's not my design, and I wouldn't charge you for labor either, I enjoyed building it tremendously, it was like a "big boys' lego" for me... ;-) You can check out my "build log" as another "issue": https://github.com/lhm0/rotating_display_color/issues/4

Closed 2025-03-24.

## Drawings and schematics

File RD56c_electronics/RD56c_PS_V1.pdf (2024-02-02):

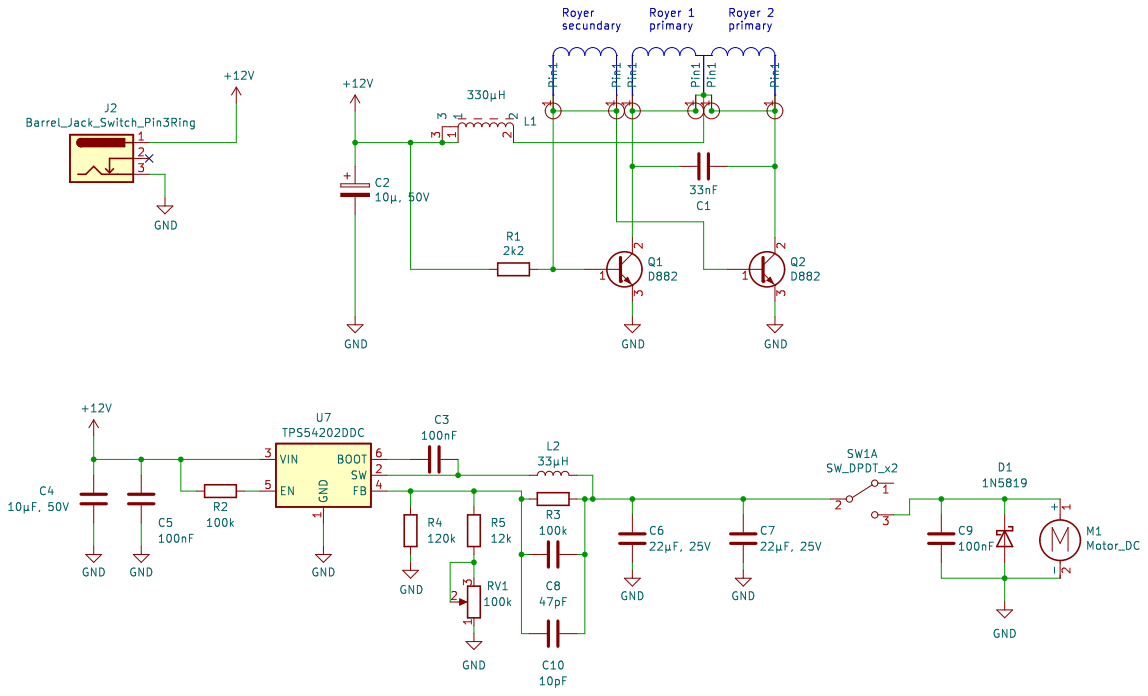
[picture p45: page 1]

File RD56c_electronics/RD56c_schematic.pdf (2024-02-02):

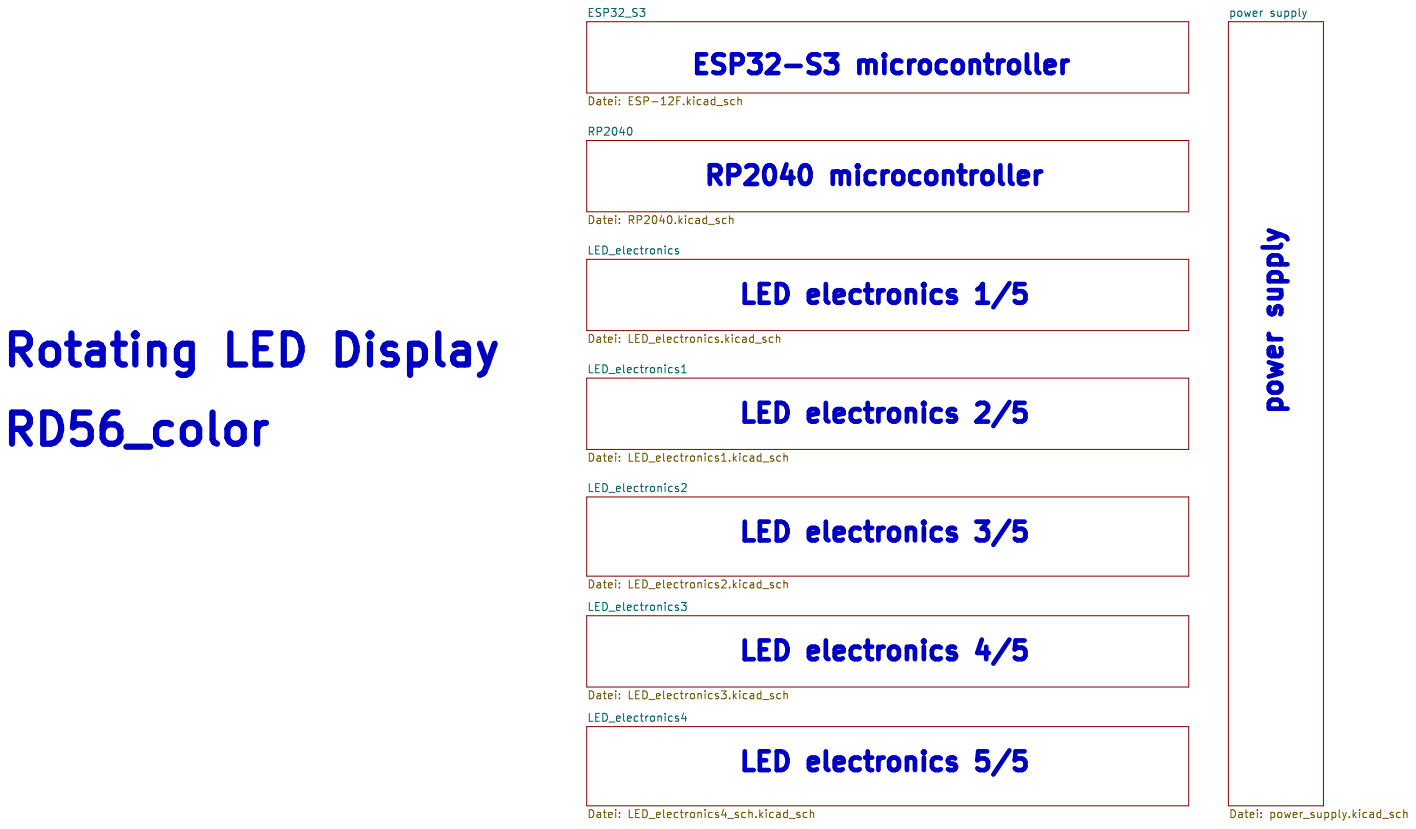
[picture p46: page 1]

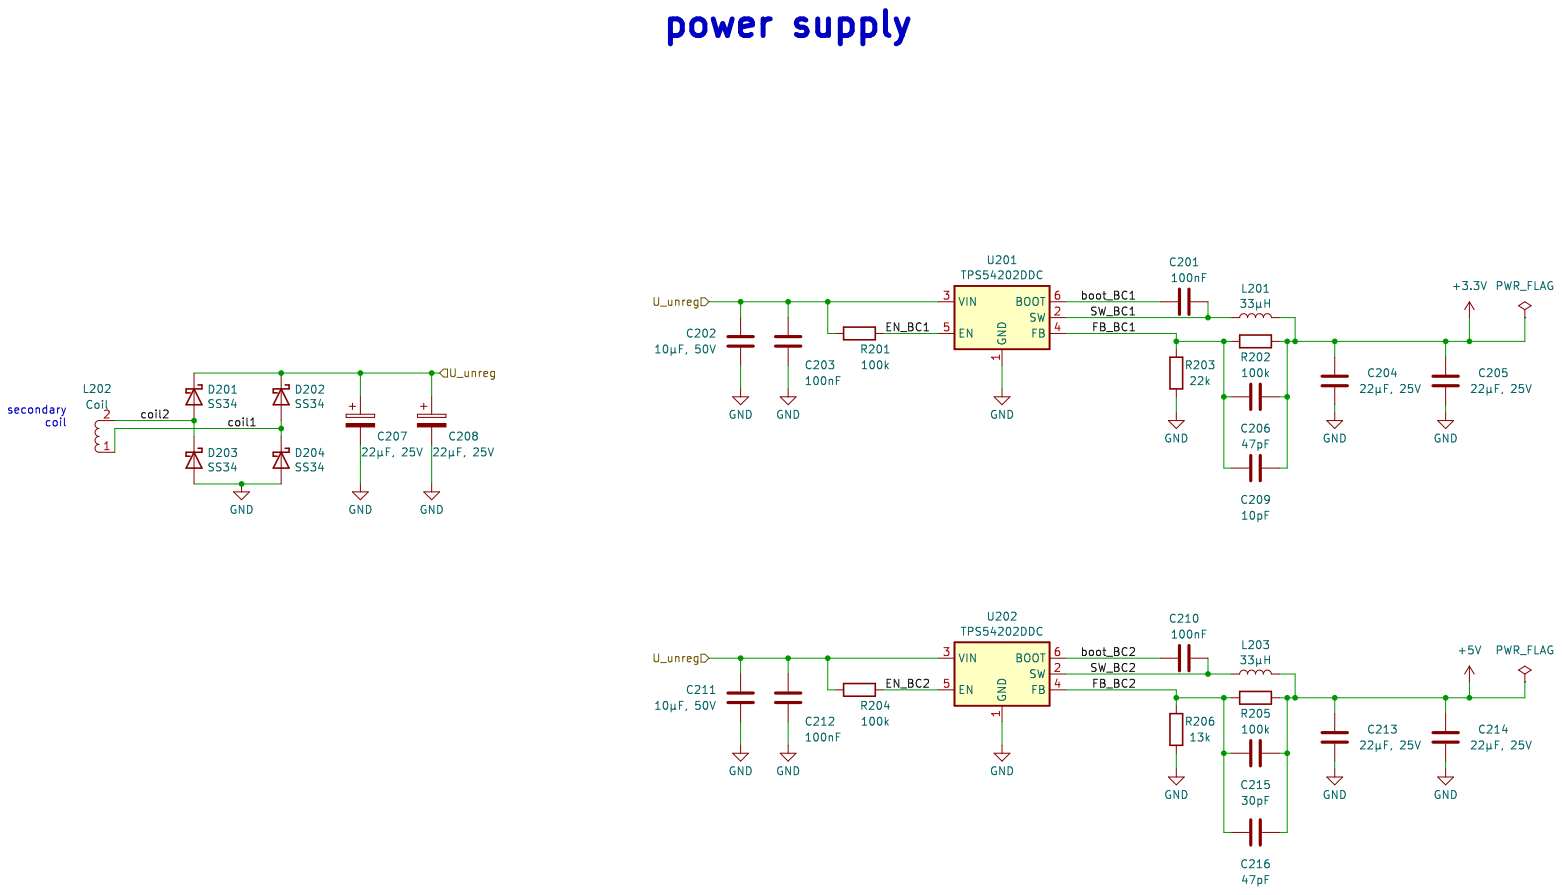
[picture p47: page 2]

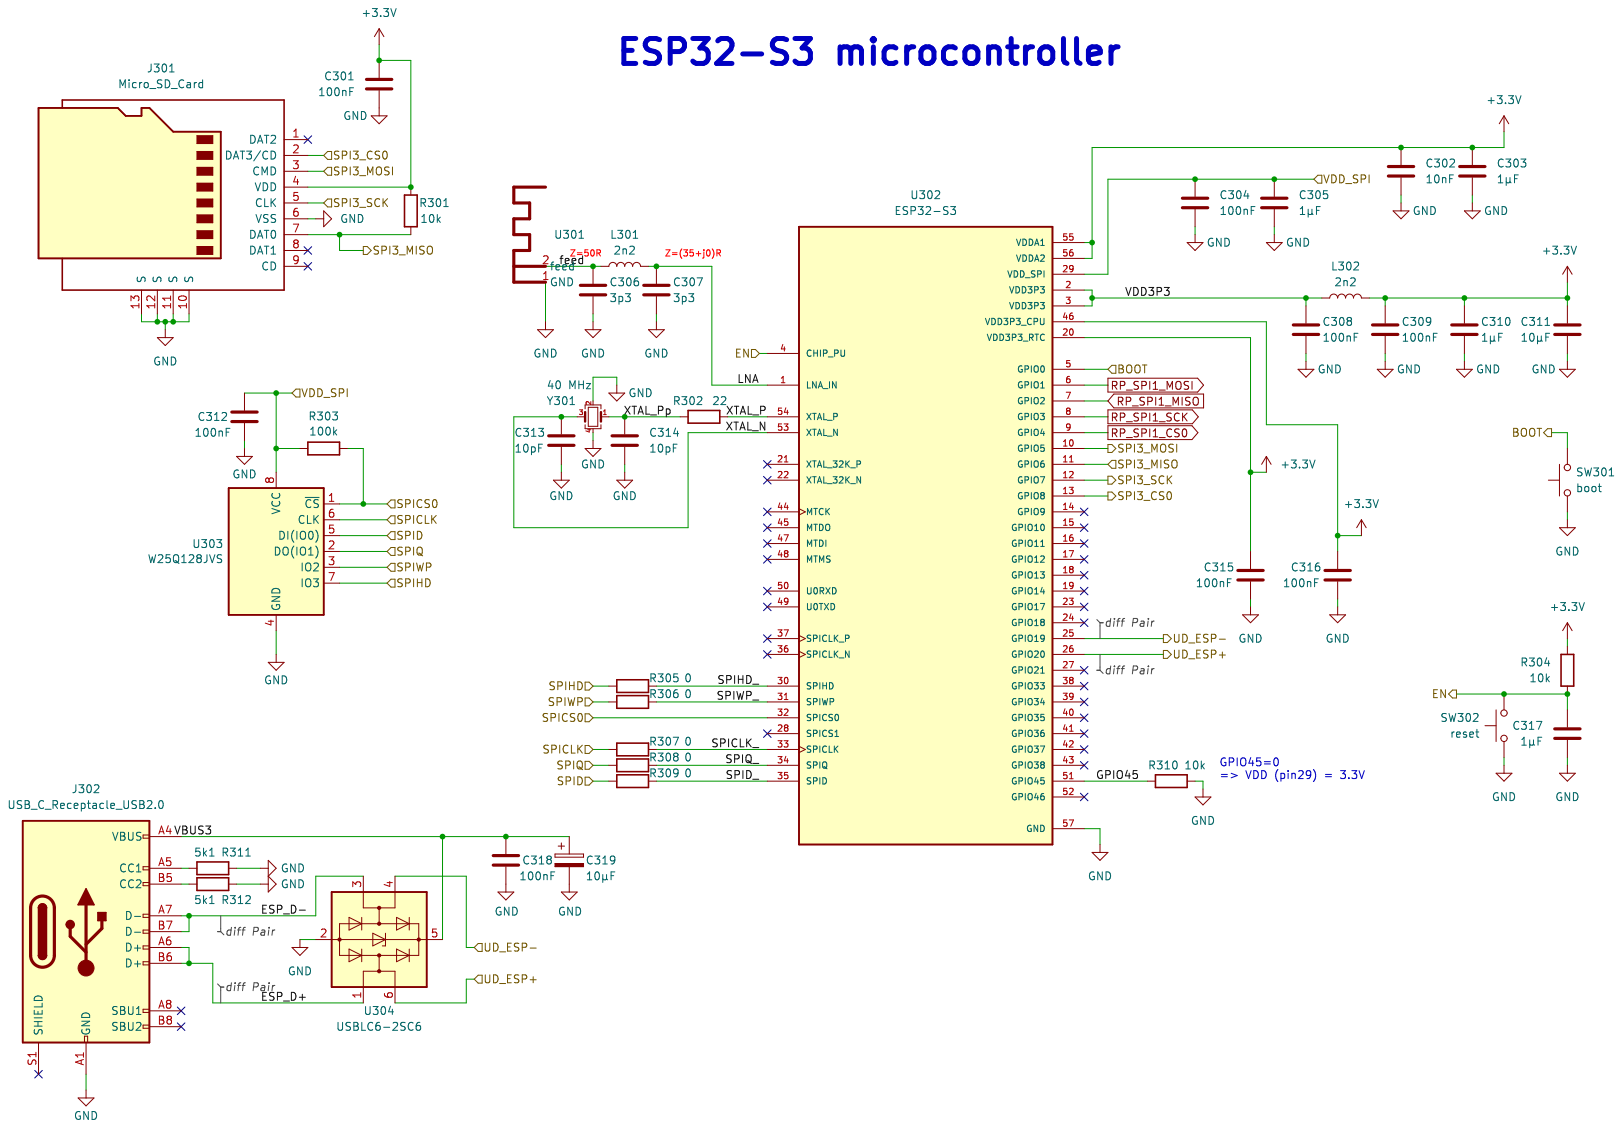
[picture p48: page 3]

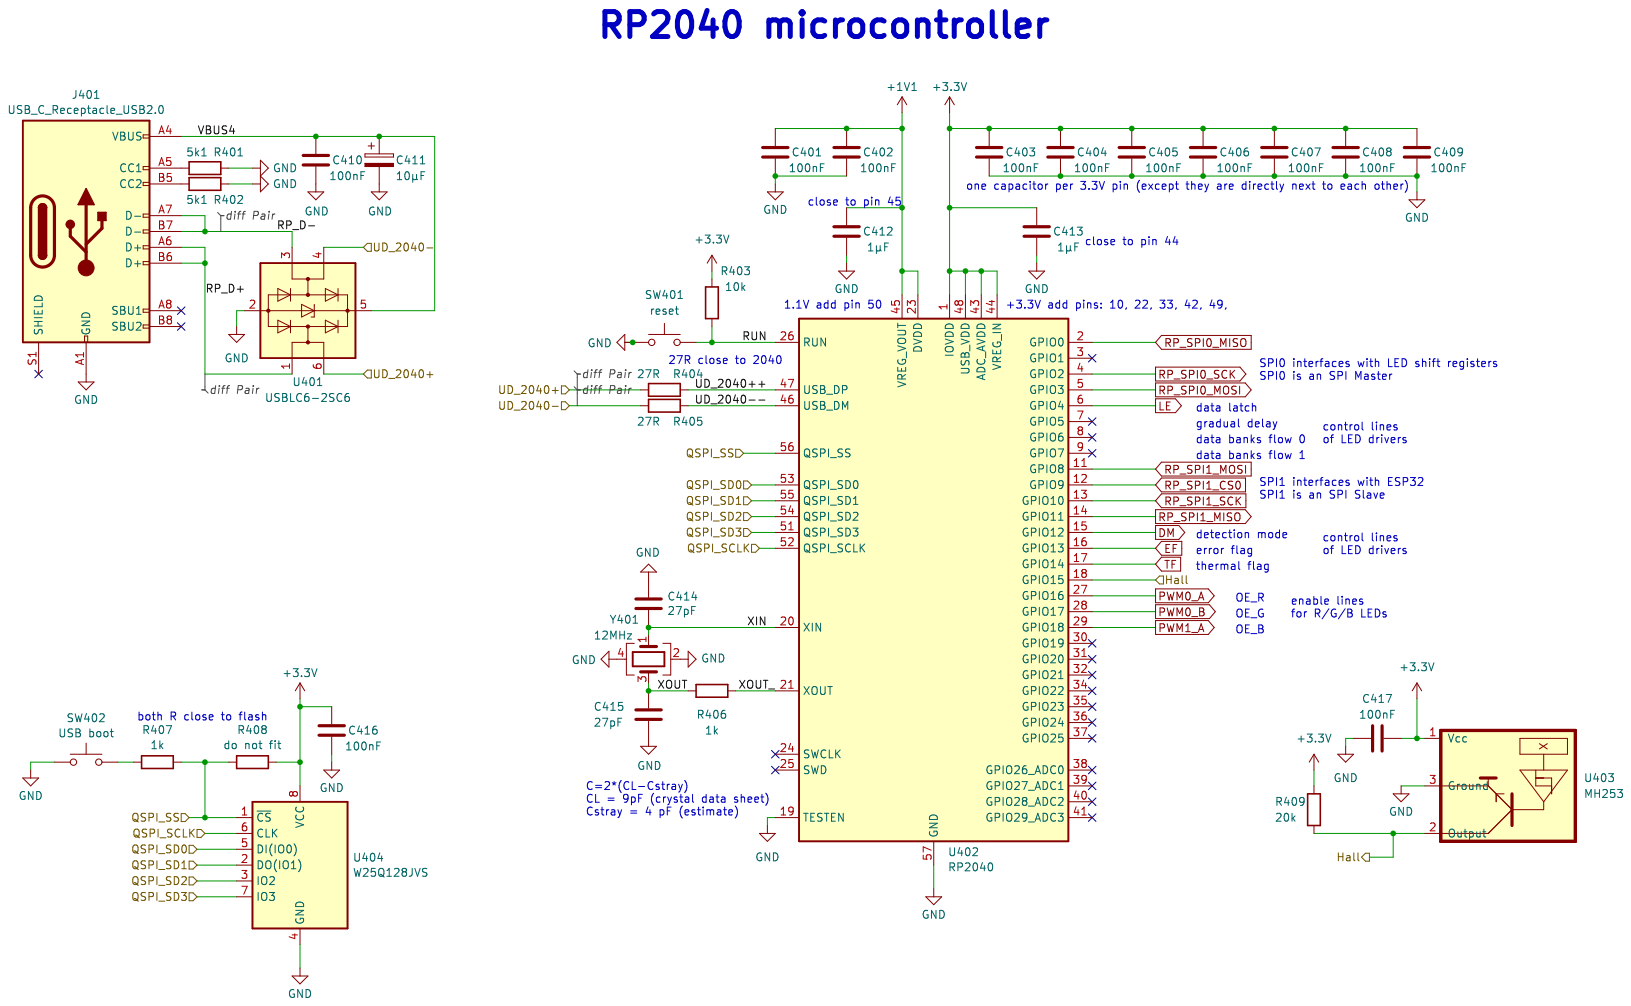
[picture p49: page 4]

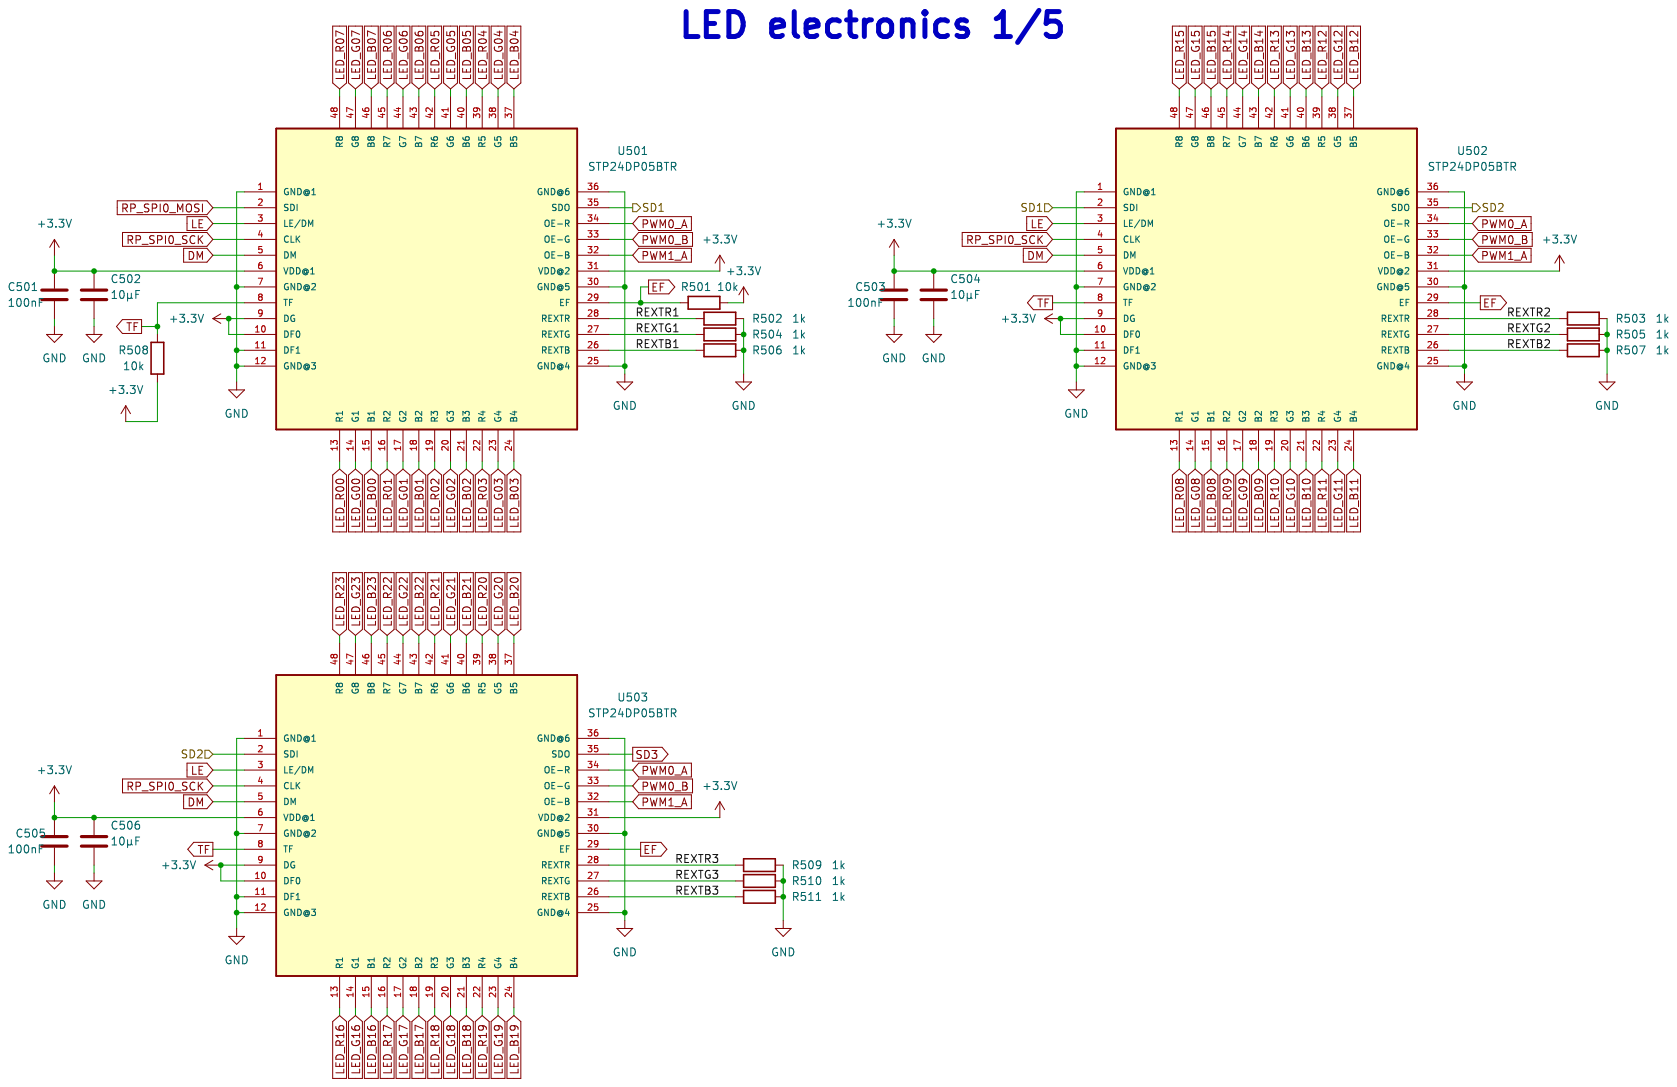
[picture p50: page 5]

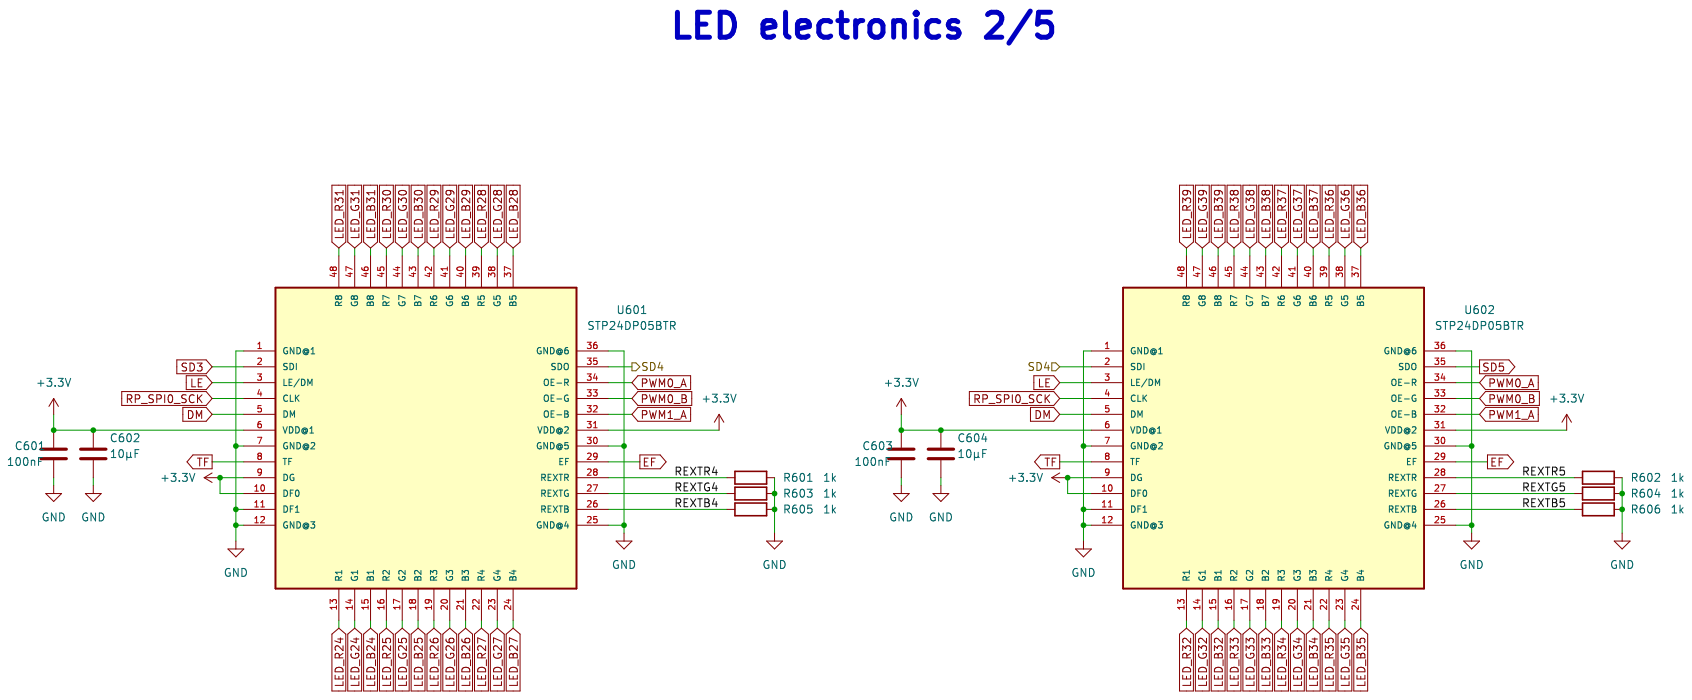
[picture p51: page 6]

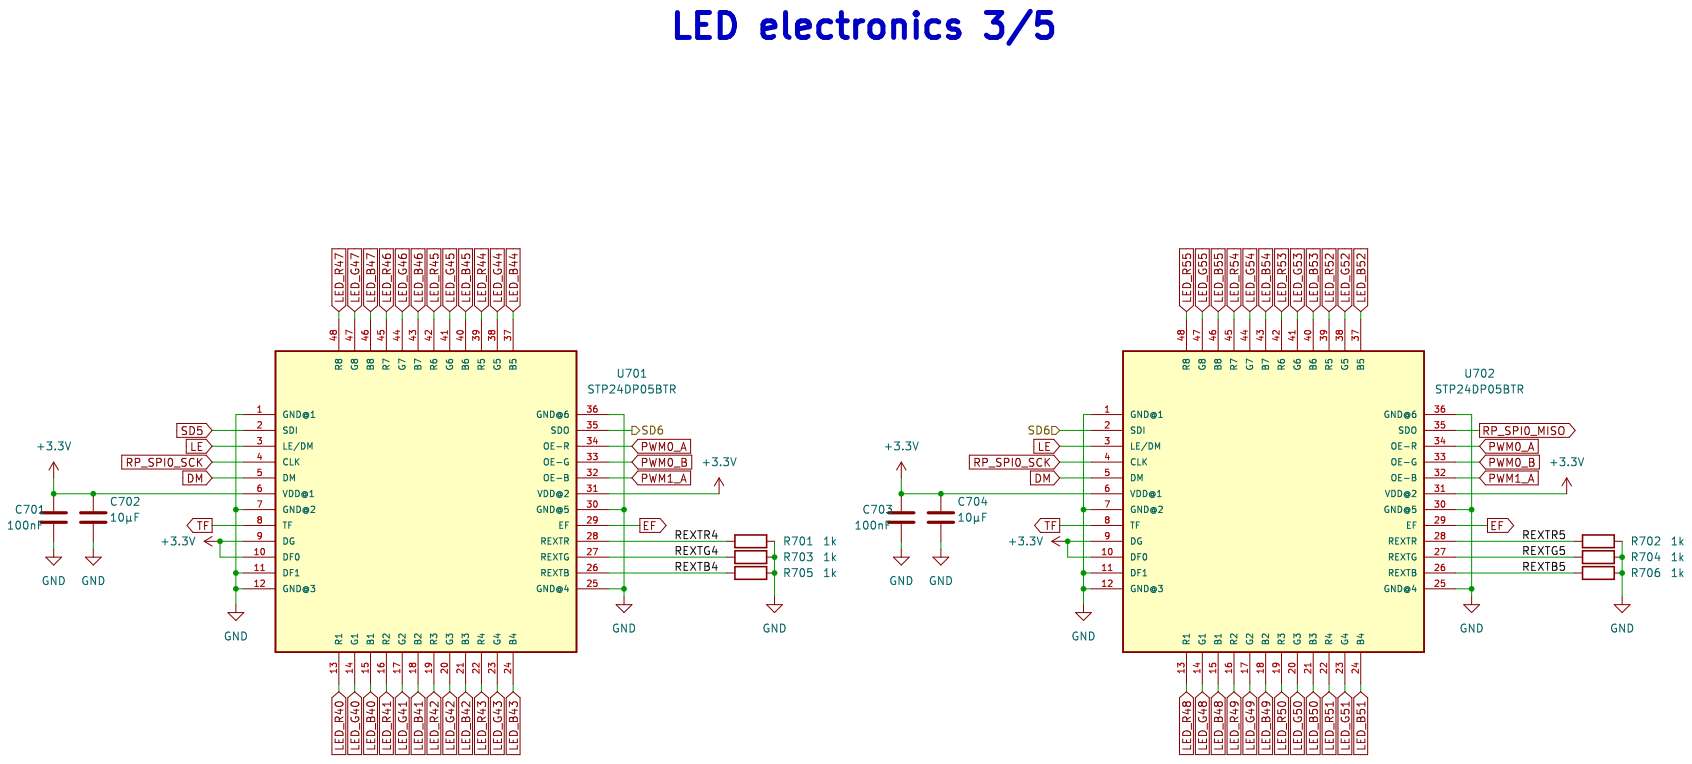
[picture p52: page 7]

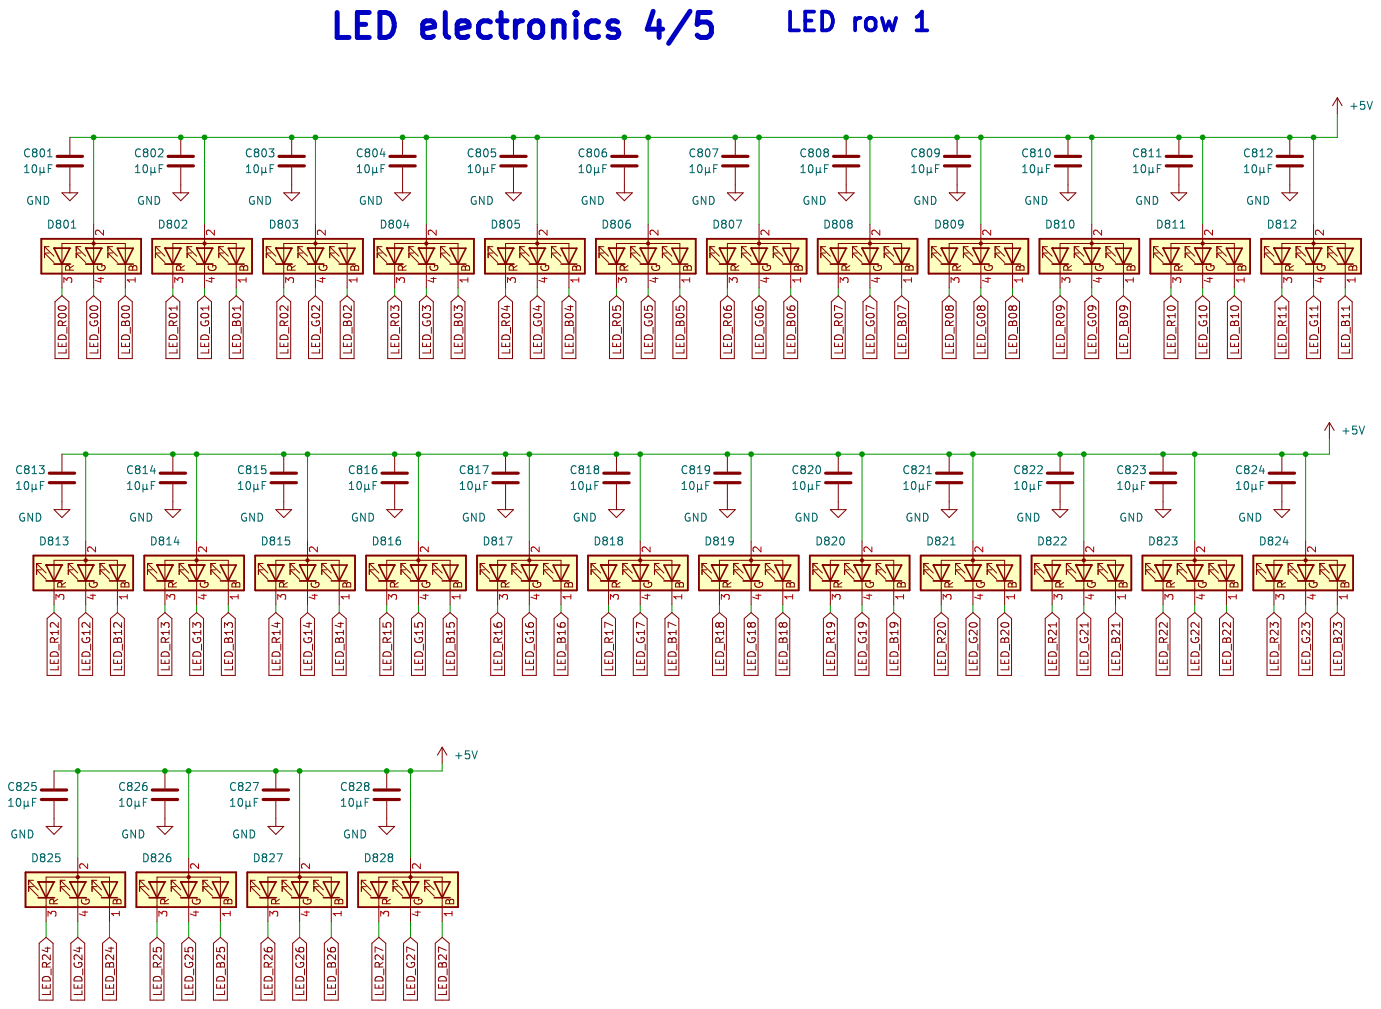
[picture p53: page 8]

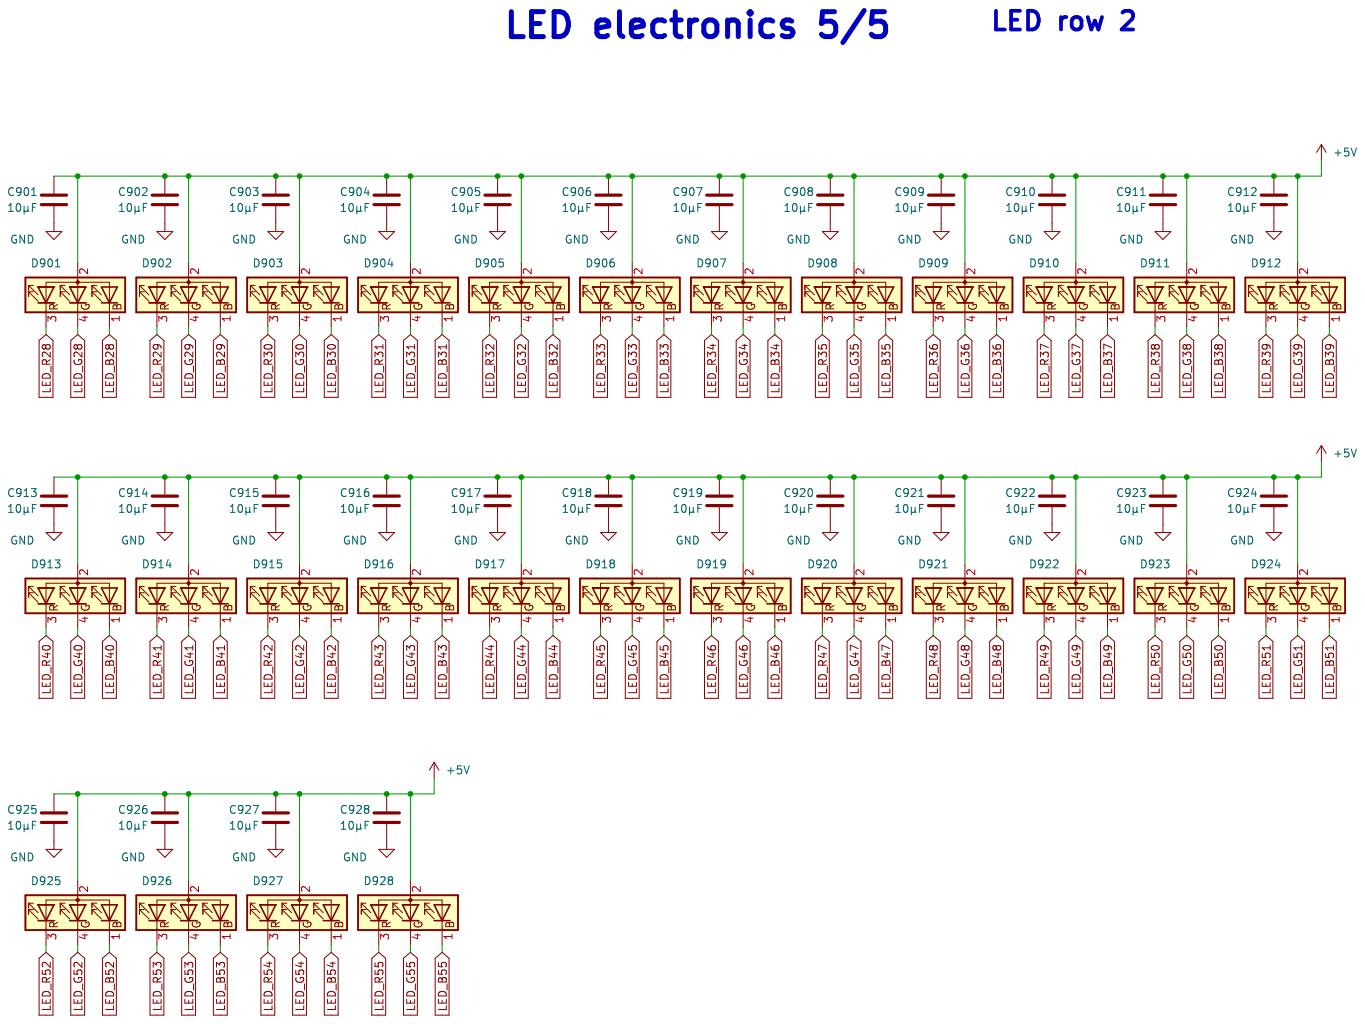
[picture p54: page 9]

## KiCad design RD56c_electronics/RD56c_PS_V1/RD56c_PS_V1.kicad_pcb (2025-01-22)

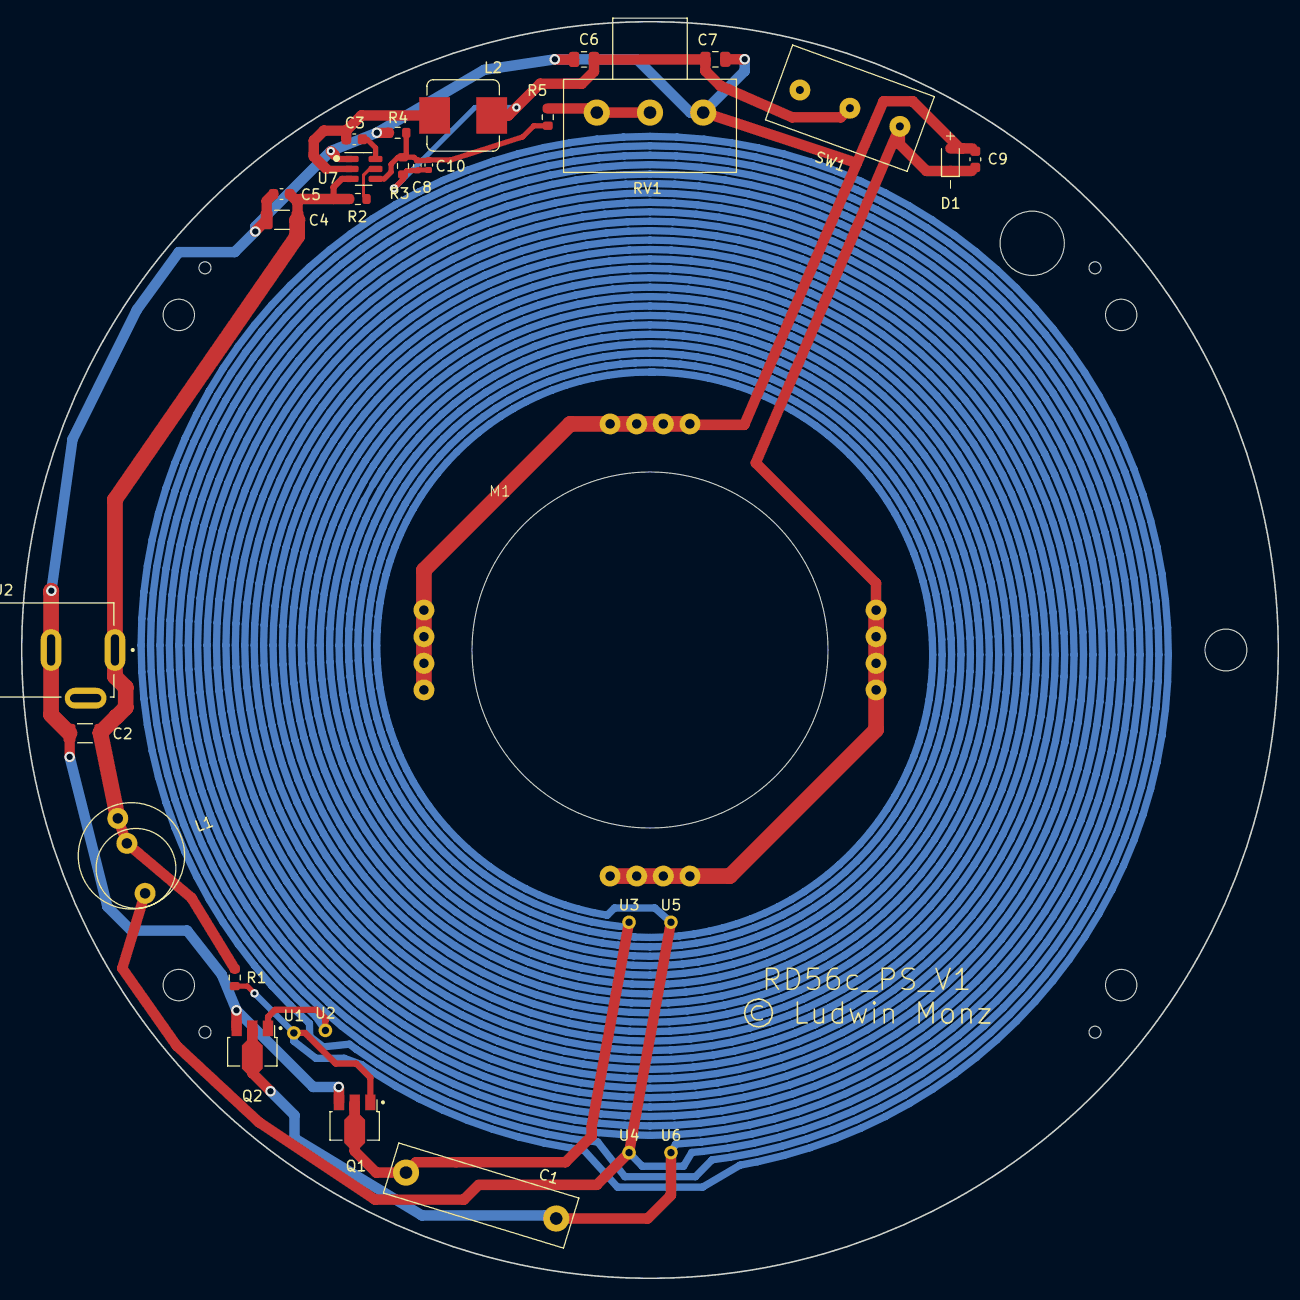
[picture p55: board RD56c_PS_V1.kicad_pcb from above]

Board: 2 copper layers, 120.0 x 120.0 mm, 31 parts (0 on the bottom side), 11 nets.

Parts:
C1: 33nF; MKP10_630V
C2: 10µ, 50V; C_1206_3216Metric
C3, C5, C9: 100nF; C_0603_1608Metric
C4: 10µF, 50V; C_1206_3216Metric
C6, C7: 22µF, 25V; C_0805_2012Metric
C8: 47pF; C_0402_1005Metric
C10: 10pF; C_0402_1005Metric
D1: 1N5819
J2: Barrel_Jack_Switch_Pin3Ring; GRAVITECH_CON-SOCJ-2155
L1: 330µH; L_vertical12
L2: 33µH; L_Bourns_SRP7028A_7.3x6.6mm
M1: Motor_DC; motor_tray
Q1, Q2: D882
R1: 2k2; R_0603_1608Metric
R2, R3: 100k; R_0603_1608Metric
R4: 120k; R_0603_1608Metric
R5: 12k; R_0603_1608Metric
RV1: 100k; Poti_10mm
SW1: SW_DPDT_x2; Switch1
U1, U2, U3, U4, U5, U6: Pin-Connector; Pin_2mm
U7: TPS54202DDC; SOT-23-6

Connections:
+12V: C2.1, C4.1, C5.1, J2.1, L1.1, L1.3, R1.2, R2.1, U7.3 (VIN)
GND: C2.2, C4.2, C5.2, C6.2, C7.2, C9.2, D1.2 (A), J2.3, M1.2 (-), Q1.3 (E), Q2.3 (E), R4.2, RV1.1, U7.1 (GND)
unnamed: C9.1, D1.1 (K), M1.1 (+), SW1.3 (C)
unnamed: Q1.1 (B), Q2.1 (B), R1.1, U1.1 (Pin1), U2.1 (Pin1)
unnamed: C1.1, C1.2, L1.2, Q1.2 (C), Q2.2 (C), U3.1 (Pin1), U4.1 (Pin1), U5.1 (Pin1), U6.1 (Pin1)
unnamed: R5.2, RV1.2, RV1.3
unnamed: C6.1, C7.1, C8.1, C10.1, L2.2, R3.2, SW1.2 (B)
unnamed: C3.1, U7.6 (BOOT)
unnamed: R2.2, U7.5 (EN)
unnamed: C8.2, C10.2, R3.1, R4.1, R5.1, U7.4 (FB)
unnamed: C3.2, L2.1, U7.2 (SW)

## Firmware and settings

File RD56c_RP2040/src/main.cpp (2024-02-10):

// =========================================================================================================================================
//                                                 Rotating Color Display RD56c
//                                                    © Ludwin Monz
// License: Creative Commons Attribution - Non-Commercial - Share Alike (CC BY-NC-SA)
// you may use, adapt, share. If you share, "share alike".
// you may not use this software for commercial purposes 
// =========================================================================================================================================


#include <Arduino.h>
#include "pico/stdlib.h"
#include "hardware/pwm.h"
#include "hardware/spi.h"

#define PWM0_A 16					// enable R LEDs
#define PWM0_B 17					// enable G LEDs
#define PWM1_A 18					// enable B LEDs

#define SPI0_MISO 0					// LED SPI (STP24DP05)
#define SPI0_CSO 1					// RP2040 is SPI master
#define SPI0_SCK 2
#define SPI0_MOSI 3

#define SPI1_MOSI 8					// SPI for ESP32 - RP2040 communication
#define SPI1_CSO 9					// RP2040 is SPI slave
#define SPI1_SCK 10
#define SPI1_MISO 11

#define LE 4						// control lines for STP24DP05
#define DG 5
#define DF0 6
#define DF1 7

#define DM 12
#define EF 13
#define TF 14
#define Hall 15						// Hall sensor input

#define lpt 1920					// lines per turn

#define BUF_LEN 128
#define SPI_RW_LEN 1
#define SPI1_BLOCK_SIZE 40320		// 1920 * 7 * 3

void PixelIRQ();											// declare PixelIRQ handler
void SPIIRQ();												// declare SPIIRQ handler
void HallIRQ(uint gpio, uint32_t events);					// declare HallIRQ Handler

void startPattern();										// populates line[][][] with initial values

unsigned int brightnessCalc();								// computes off periode

uint8_t line[1921][7][3];									// [pixel row] [7x8=56 LEDs] [RGB] [alternate]
uint8_t line_rcv[1921][7][3][2];							// received data is stored in this array. [2] dimension is used for alternating use
int rcv_bank = 0;											// bank of line_rcv being used for storage of received data
int use_bank = 1;											// bank of line_rcv being used for compying to line[][][]

int brightness;												// 0...100

uint8_t spi0_wBuff[21];										// write buffer for SPI0
uint8_t spi1_in_buf[BUF_LEN];

int line_counter0 = 960;       								// counts the displayed lines. line_counter0 is 1/2turn ahead of line_counter1
int line_counter1 = 0;        								//

long LPT = lpt;												// lines per turn

unsigned int line_period = 30000; 							// time per line
unsigned int off_period = 29950;
int line_offset = 700;        								// clock orientation (12 is up); depends on where the trigger LED is positioned

long tpt = 0;												// time oer turn	

bool msg = false;									//

int SPI1_index_i = 0;										// index of SPI1 block transmission
int SPI1_index_j = 0;										//
int SPI1_index_k = 0;										//

void setup() {
	LPT = lpt;
	line_counter0=LPT/2;
// ====================================================================================================================
//
//										setup for STP24DP05 control lines
//
// ====================================================================================================================

	gpio_init(LE);											// set LE as output
	gpio_set_dir(LE, true);
	gpio_put(LE, 0);										// set LE to 0 => hold value

	gpio_init(DG);											// set DG as output
	gpio_set_dir(DG, true);
	gpio_put(DG, 1);										// gradual delay = 0 => activate

	gpio_init(DF0);											// set DF0 as output
	gpio_set_dir(DF0, true);
	gpio_put(DF0, 1);										// data flow: RGB

	gpio_init(DF1);											// set DF1 as output
	gpio_set_dir(DF1, true);
	gpio_put(DF1, 0);										// data flow: RGB

	gpio_init(EF);											// set DF1 as input
	gpio_set_dir(EF, false);

	gpio_init(TF);											// set DF1 as input
	gpio_set_dir(TF, false);

	gpio_init(DM);											// set DM as output
	gpio_set_dir(DM, true);
	gpio_put(DM, 1);

	gpio_init(Hall);
	gpio_set_dir(Hall, false);								// Hall is an input
	gpio_pull_up(Hall);										// switch on pull up resistor


// ====================================================================================================================
//
//										setup PWM for LED control
//
//	at maximum speed, display spins @ 50 Hz
//  time per turn = 20ms
//	time per line = 20ms/1980 lines/turn = 10 µs
//  pwm counts per line = 10 µs * 125 MHz = 1260
//
// ====================================================================================================================

	gpio_init(PWM0_A);										// set gpio as output
	gpio_set_dir(PWM0_A, true);								//
	gpio_init(PWM0_B);										// set gpio as output
	gpio_set_dir(PWM0_B, true);								//
	gpio_init(PWM1_A);										// set gpio as output
	gpio_set_dir(PWM1_A, true);								//

	gpio_set_function(PWM0_A, GPIO_FUNC_PWM);				// enable PWM on 3 pins
	gpio_set_function(PWM0_B, GPIO_FUNC_PWM);
	gpio_set_function(PWM1_A, GPIO_FUNC_PWM);

	pwm_set_wrap (0, line_period);							// upper threshold of counter 0
	pwm_set_phase_correct (0, false);						// counter 0 will reset to 0, once upper threshold is reached
	
	pwm_set_wrap (1, line_period);							// upper threshold of counter 1
	pwm_set_phase_correct (1, false);						// counter 1 will reset to 0, once upper threshold is reached

	pwm_set_clkdiv_int_frac(0, 1, 0);					    // set divisor for clock divider (system clock = 125 MHz)
	pwm_set_clkdiv_int_frac(1, 1, 0);	

	pwm_set_chan_level(0, 0, off_period);					// level is the mid threshold, when the output goes to zero
	pwm_set_chan_level(0, 1, off_period);					// level is the mid threshold, when the output goes to zero
	pwm_set_chan_level(1, 0, off_period);					// level is the mid threshold, when the output goes to zero

	pwm_set_enabled (0, true);								// enable PWM slice 0 (output pins 16 and 17)
	pwm_set_enabled (1, true);								// enable PWM slice 1 (output pins 18)

	irq_set_exclusive_handler(PWM_IRQ_WRAP, PixelIRQ);		// attach PixelIRQ() to the PWM interrupt
	irq_set_enabled(PWM_IRQ_WRAP, true);					// enanble irq

	startPattern();

// ====================================================================================================================
//
//										setup SPI for data transfer to LEDs
//
//	bits per line: 40 LEDs x 3 = 120 bits (15 bytes)
//	SPI clock frequency: 25 MHz (maximum defined by LED driver chip)
//	time per data transmission: 120 / 25 MHz = 4.8 µs
// 	==> time for data transfer matches minimum time per line (10 µs)
//
// ====================================================================================================================

	spi_init(spi0,25*1000*1000);										// initialize SPI0, set baudrate to 25 MHz (maximum of STP24DP05)
	spi_set_slave(spi0, false);											// initialize SPI0 as master
	spi_set_format(spi0, 8, SPI_CPOL_0, SPI_CPHA_0, SPI_MSB_FIRST);		// 8 data bits, data latched on first clock transition, clock active high

	gpio_set_function(SPI0_MOSI, GPIO_FUNC_SPI);						// initialize SPI0 pins
	gpio_set_function(SPI0_CSO, GPIO_FUNC_SPI);
	gpio_set_function(SPI0_SCK, GPIO_FUNC_SPI);
	gpio_set_function(SPI0_MISO, GPIO_FUNC_SPI);


// ====================================================================================================================
//
//										setup interrupt handler for Hall trigger
//
// ====================================================================================================================

	gpio_set_function(Hall, GPIO_FUNC_SIO);								// software IO control (SIO)
	gpio_set_irq_enabled_with_callback(Hall, GPIO_IRQ_EDGE_FALL, true, &HallIRQ);

	pwm_clear_irq(0);										// clear pwm interrupt
	pwm_set_irq_enabled(0, true);							// enable pwm interrupt

	Serial.begin(115200);
}


void setup1() {

// ====================================================================================================================
//
//										setup SPI for data transfer ESP32 => RP2040
//			  							 The SPI1 interrupt is handled bei core1 !
//
// ====================================================================================================================

	spi_init(spi1,1000*1000);												//
	spi_set_slave(spi1, true);											// initialize SPI1 as slave

	gpio_set_function(SPI1_MOSI, GPIO_FUNC_SPI);						// initialize SPI1 pins
	gpio_set_function(SPI1_CSO, GPIO_FUNC_SPI);
	gpio_set_function(SPI1_SCK, GPIO_FUNC_SPI);
	gpio_set_function(SPI1_MISO, GPIO_FUNC_SPI);

	spi1_hw -> imsc = 0x06;								    // enable the RX FIFO interrupt (RXIM) and RXtimeout (RTIM)
	irq_set_exclusive_handler(SPI1_IRQ, SPIIRQ);			// attach SPIIRQ() to the SPI1 interrupt
	irq_set_enabled(SPI1_IRQ, true);						// enanble irq

}


void loop() {
		Serial.print("brightness: ");
		Serial.println(brightness);
		delay(1000);
}

// ================================================================================================================
//
//													Pixel IRQ
//	this interrupt routine is triggered by the PWM counter, when the TOP value is reached. it outputs the new LED 
// 	data via SPI.
// 	the LED data is constantly (and asynchroyously) updated via the second SPI interface (SPIIRQ()). In order to avoid
// 	disturbances of the image, the first LED row uses the up-to-date data from line_rcv[][][][], while the second LED row
// 	uses buffered data from line[][][]. When ever new data is send to the first row, the corresponding data for the
// 	second row (which will only be needed half a turn later) is stored in the line[][][] buffer. 
// 	
// ================================================================================================================

void PixelIRQ() {

	tpt+=line_period;

	for (int b = 0; b<7; b++) {
		for (int c = 0; c<3; c++) line[line_counter0][b][c] = line_rcv[line_counter0][b][c][use_bank];
	}

	spi0_wBuff[0]=line_rcv[line_counter1][6][2][use_bank];		//R
	spi0_wBuff[1]=line_rcv[line_counter1][6][1][use_bank];		//G	
	spi0_wBuff[2]=line_rcv[line_counter1][6][0][use_bank];		//B
	spi0_wBuff[3]=line_rcv[line_counter1][5][2][use_bank];		//R
	spi0_wBuff[4]=line_rcv[line_counter1][5][1][use_bank];		//G	
	spi0_wBuff[5]=line_rcv[line_counter1][5][0][use_bank];		//B
	spi0_wBuff[6]=line_rcv[line_counter1][4][2][use_bank];		//R
	spi0_wBuff[7]=line_rcv[line_counter1][4][1][use_bank];		//G	
	spi0_wBuff[8]=line_rcv[line_counter1][4][0][use_bank];		//B
	spi0_wBuff[9]=(line[line_counter0][3][2] & 0xF) + (line_rcv[line_counter1][3][2][use_bank] & 0xF0);		//R
	spi0_wBuff[10]=(line[line_counter0][3][1] & 0xF) + (line_rcv[line_counter1][3][1][use_bank] & 0xF0);	//G
	spi0_wBuff[11]=(line[line_counter0][3][0] & 0xF) + (line_rcv[line_counter1][3][0][use_bank] & 0xF0);	//B
	spi0_wBuff[12]=line[line_counter0][2][2];		//R
	spi0_wBuff[13]=line[line_counter0][2][1];		//G	
	spi0_wBuff[14]=line[line_counter0][2][0];		//B
	spi0_wBuff[15]=line[line_counter0][1][2];		//R
	spi0_wBuff[16]=line[line_counter0][1][1];		//G	
	spi0_wBuff[17]=line[line_counter0][1][0];		//B
	spi0_wBuff[18]=line[line_counter0][0][2];		//R
	spi0_wBuff[19]=line[line_counter0][0][1];		//G	
	spi0_wBuff[20]=line[line_counter0][0][0];		//B
	
	int n = spi_write_blocking(spi0, spi0_wBuff, 21);		// send 21 bytes

	gpio_put(LE, 1);									// set LE to 1 => update LED output
	gpio_put(LE, 0);									// set LE to 0 => hold value

	line_counter0++;
    if (line_counter0 > (LPT-1)) {
		line_counter0 = 0;	
	}
	
    line_counter1++;
    if (line_counter1 > (LPT-1)) {
		line_counter1 = 0;
	}

	pwm_clear_irq(0);										// clear interrupt

}

// ====================================================================================================================
//
//														HallIRQ
//
//	The Hall sensor triggers this routine, when a full turn of the display is completed. The time-per-turn (tpt) is 
//	used to re-calculate the correct time per line (line_period). The PWM couners are updated accordingly.
//
// ====================================================================================================================


void HallIRQ(uint gpio, uint32_t events) {
	tpt = tpt + pwm_get_counter(0);

	long new_line_period = tpt/LPT;

	if (new_line_period>65500) new_line_period = 65500;

  	if(labs(new_line_period-line_period)>4) {
      	line_period = new_line_period;             				// when motor starts spinning, tpt changes very much from turn to turn.
  	} 
	else {
      	line_period = (15*line_period+new_line_period)/16;        // in this case correct line_period fully. Otherwise make small corrections, only.
  	}

//	off_period = brightnessCalc();        			// 
	off_period = (unsigned int)((float)line_period * (1.0 - ((float)brightness*(float)brightness/50000.0)));
//	if ((line_period - off_period)<(95*line_period/100)) off_period = 95*line_period/100;

  	pwm_set_wrap (0, line_period);							// upper threshold of counter 0
	pwm_set_wrap (1, line_period);							// upper threshold of counter 1

	pwm_set_chan_level(0, 0, off_period);					// level is the mid threshold, when the output goes to zero
	pwm_set_chan_level(0, 1, off_period);					// level is the mid threshold, when the output goes to zero
	pwm_set_chan_level(1, 0, off_period);					// level is the mid threshold, when the output goes to zero

 	tpt = 0;
  	line_counter1 = line_offset;  							// restart line_counter
  	line_counter0 = line_offset + LPT/2;

  	if (line_counter0 >= LPT) line_counter0 = line_counter0-LPT;
  
}


// ====================================================================================================================
//
//																SPIIRQ()
// 	interrupt routine for handling incoming data at SPI1. This routine runs in core 1 in order not to interfere with 
//	time critical PixelIRQ.
//	The received data is stored in line_rcv[][][][bank], while there are two banks (0 and 1), which are used 
//	alternatingly. This avoids the display of incomplete data.
//
// ====================================================================================================================

void SPIIRQ() {
	while (spi_is_readable(spi1)) {							// read FIFO until empty
		spi_read_blocking (spi1, 0, &line_rcv[SPI1_index_i][SPI1_index_j][SPI1_index_k][rcv_bank], 1);
		SPI1_index_i++;
		if (SPI1_index_i >= 1921) {
			SPI1_index_i=0;
			SPI1_index_j++;
			if (SPI1_index_j >= 7) {
				SPI1_index_j=0;
				SPI1_index_k++;
				if (SPI1_index_k >= 3) {
					SPI1_index_k = 0;
				}
			}
		}
		if ((SPI1_index_i == 0) & (SPI1_index_j == 0) & (SPI1_index_k == 0)) {
			brightness = (int)line_rcv[1920][0][0][rcv_bank];
			use_bank = rcv_bank;
			rcv_bank++;
			if (rcv_bank > 1) rcv_bank = 0;
		}
	}
}



void startPattern() {
	int i, j;
	for (i=0; i<(LPT/3); i++) {
		for (j=0; j<7; j++) {
			line_rcv[i][j][0][1] = 0xFF;							// R
			line_rcv[i][j][1][1] = 0;								// G
			line_rcv[i][j][2][1] = 0;								// B
			line_rcv[i+(LPT/3)][j][0][1] = 0;
			line_rcv[i+(LPT/3)][j][1][1] = 0xFF;
			line_rcv[i+(LPT/3)][j][2][1] = 0;
 			line_rcv[i+(LPT*2/3)][j][0][1] = 0;
			line_rcv[i+(LPT*2/3)][j][1][1] = 0;
			line_rcv[i+(LPT*2/3)][j][2][1] = 0xFF;
		}
	}
}


unsigned int brightnessCalc() {
	float factor = (1-(((float)brightness*(float)brightness)/10000.0+0.09)*0.1);
	Serial.print("brightness factor: ");
	Serial.println(factor);
	return (unsigned int)(line_period*factor);  
}

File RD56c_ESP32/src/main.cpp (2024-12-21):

// =========================================================================================================================================
//                                                 Rotating Display RD56c
//                                                    © Ludwin Monz
// License: Creative Commons Attribution - Non-Commercial - Share Alike (CC BY-NC-SA)
// you may use, adapt, share. If you share, "share alike".
// you may not use this software for commercial purposes 
// =========================================================================================================================================


#include <Arduino.h>

#include "my_ESP.h"
#include "RD_40.h"
#include "RD_40trafo.h"
#include "my_BMP.h"
#include "my_BMPtemplates.h"
#include "FlashFS.h"
#include "webInterface.h"

#include <WiFi.h>
#include <time.h>

// =========================================================================================================================================
// 
//                                                        Rotating Display
//
// The program uses OOP in order to structure data and functions. These are the classes:
//
// 1. my_ESP
//    description:    the class manages the resources of the ESP microcontroller. 
//    key methods:    begin()                                         configures Wifi, i2c interface, sets time 
//                    getMyTime()                                     occupies the time and date attributes (see below) 
//                    myPassword()                                    returns Wifi Password which is being used
//                    mySSID()                                        returns Wifi SSID
//    key attributes: int Sec, int Min, int Hour, ...
//
// 2. RD_40
//    description:    the class provides the central rotating display object. It manages the data of the displayed image (one bit per LED), 
//                    etc. 
//                    The class has methods for displaying bitmaps and for transferring data to the display controller. 
//    key methods:    begin()                                         initialize display mode and data transfer to the display controller
//                    upload()                                        uploads display data to the display controller
//                    displayBMP(unsigned char bmp[][14])             displays bitmap
//    key attributes: clockMode, brightness
//
// 3. my_BMP
//    description:    this class generates bitmaps for the display. It provides methods for generating clock and weather screens, 
//                    as well as printing text on bitmaps. The bitmap shall be handed over to the RD40 object. 
//    key methods:    generateBMP(int mode, tm* tm, String* ssid)     generates bitmap according to mode, time, ssid
//    key attributes: bitmap[][]                                      this is a 110x110 pixel bitmap
//
// 4. webInterface
//    description:    the class manages the web user interface. It uses the AsyncWebServer library and runs in the background without any need for
//                    attention. The class provides certain attributes, which are set by the web interface:
//    key methods:    begin(String* ssid_)                            starts AsyncWebServer. ssid is displayed (not changed) in web interface
//    key attributes: int clockMode;                                  mode 0 = IP-address, mode 1 = analog clock, mode 2 = digital clock, mode 3 = logo clock, mode 4 = weather clock
//                    int brightness;                                 brightness value in %
//                    char apiKey[50]="";                             apiKey for openweathermap.org
//                    char location[50]="";                           location for openweathermap.org
//                    char country[20]="";                            country for openweathermap.org
//
//
// =========================================================================================================================================


my_ESP myESP;                                                // create instance of my_ESP
webInterface wi56;                                           // create instance of webInterface
RD_40 RD40;                                                  // create instance of RD_40
my_BMP myBMP;                                                // create instance of my_BMP

long lastWeather;                                            // remember time of last weather updte
int lastUpdate=0;                                            // remember the second of last display update
int prevSec=0;
int prevClockMode=4;                                         // remember previous clockMode

int right = 0;

// =========================================================================================================================

void setup(){

  // Serial port for debugging purposes
  Serial.begin(115200);
    delay(1000);

  myESP.begin();                            // initiates Wifi, time
  String myssid = myESP.ssid;               // withdraw SSID
  String myIpAddress = myESP.ipAddress;
  wi56.begin(myssid);                       // start web server

  myESP.getMyTime();
  Serial.printf("Zeit: %d:%d:%d\n", myESP.Hour, myESP.Min, myESP.Sec);

  RD40.begin();                             // initiate RD40 object
}

void loop() {
// +++++++++++++++++++++++++++++++++++++++++++++++++++++++++++++++++++++++++++++++++++++++++++++++++
// 
//

  if ( (((millis()-lastWeather)>60000)&&(wi56.clockMode==4)) || wi56.updateWeather) {     // update weather every 60 seconds OR if update requested with update_weather
    lastWeather=millis();
    Serial.println("request weather data.....");
    myBMP.getWeather(wi56.apiKey, wi56.location);
    wi56.updateWI(myBMP.w_icon, myBMP.w_temp, myBMP.w_humi);                               //send data via WebSocket to webpage

    wi56.updateWeather=false;
  }

  myESP.getMyTime();
  if (myESP.Sec!=prevSec) {
    prevSec = myESP.Sec;
    Serial.printf("%d:%d:%d   %d.%d.%d\n", myESP.Hour, myESP.Min, myESP.Sec, myESP.Mday, myESP.Mon, myESP.Year );
  }

long stamp = millis();                                           // current time
  if ((stamp-lastUpdate)>100) {
    lastUpdate = stamp;
    tm* mytm = &myESP.tm1; 

    myBMP.generateBMP(wi56.clockMode, mytm, myESP.ssid.c_str(), myESP.ipAddress.c_str());  // generate bitmap

    unsigned char (*mybitmap)[165] = myBMP.bitmap;                     // pointer at bitmap array

    RD40.displayBMP(mybitmap);                                        // update display data according to bitmap

    int mybrightness = wi56.brightness;                               // wi56 holds the brightness setting of user interface
    RD40.upload(mybrightness);                                          // 
  }

  wi56.update();
}

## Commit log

2024-02-04 BOM added
    [bom rotating color led display.xlsx, bom.csv, positions.csv]
2024-12-15 paths for gear.rdc and other files corrected
    [my_BMP.cpp]
2024-12-17 bug fixes, mainly file browser. some new *rdc files in /data folder
    [FlashFS.cpp, my_BMP.cpp, webInterface.cpp]
2024-12-21 move from AsyncWebServer.h to WebServer.h to fix file upload bug. Extended javascripts.
    [main.cpp, my_ESP.cpp, webInterface.cpp]
2025-01-22 added empty_sheet.kicad_wks to KiCAD folders
    [ESP-12F.kicad_sch, LED_electronics.kicad_sch, LED_electronics1.kicad_sch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]
2025-02-20 fixed type conversion error. Thx @galmiklos
    [my_ESP.cpp]
2025-03-19 added galmiklos' 3D printable case
    [RD56c-Case.FCStd, RD56c-CaseBottom.stl, RD56c-CaseTop.stl]

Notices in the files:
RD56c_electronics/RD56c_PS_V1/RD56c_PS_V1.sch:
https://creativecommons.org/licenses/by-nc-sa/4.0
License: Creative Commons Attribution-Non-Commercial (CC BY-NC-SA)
